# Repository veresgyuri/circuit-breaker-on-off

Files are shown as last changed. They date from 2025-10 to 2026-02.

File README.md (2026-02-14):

# circuit-breaker-on-off
CircuitPython test code for a spring charging motor of the high-voltage circuit breaker

**Status:** Project closed / finalized by Gyuri on 2026-02-14

**Disclaimer:**  
This is an independent, non-manufacturer document.  
See [SAFETY_AND_LEGAL.md](SAFETY_AND_LEGAL.md) for full legal and safety information.

Sorry folks, this repo comes with Hungarian comments only 🙂

# --- KÖF megszakító – felhúzómotor tesztelése ---

**Jogi figyelmeztetés:**  
Ez egy független, nem gyártói anyag.  
A teljes jogi és biztonsági információkat [itt olvashatod](SAFETY_AND_LEGAL.md).

**Az alapprobléma:**  
A rugófelhúzó egységben, idővel elreped az egyik fröccsöntött fogaskerék.

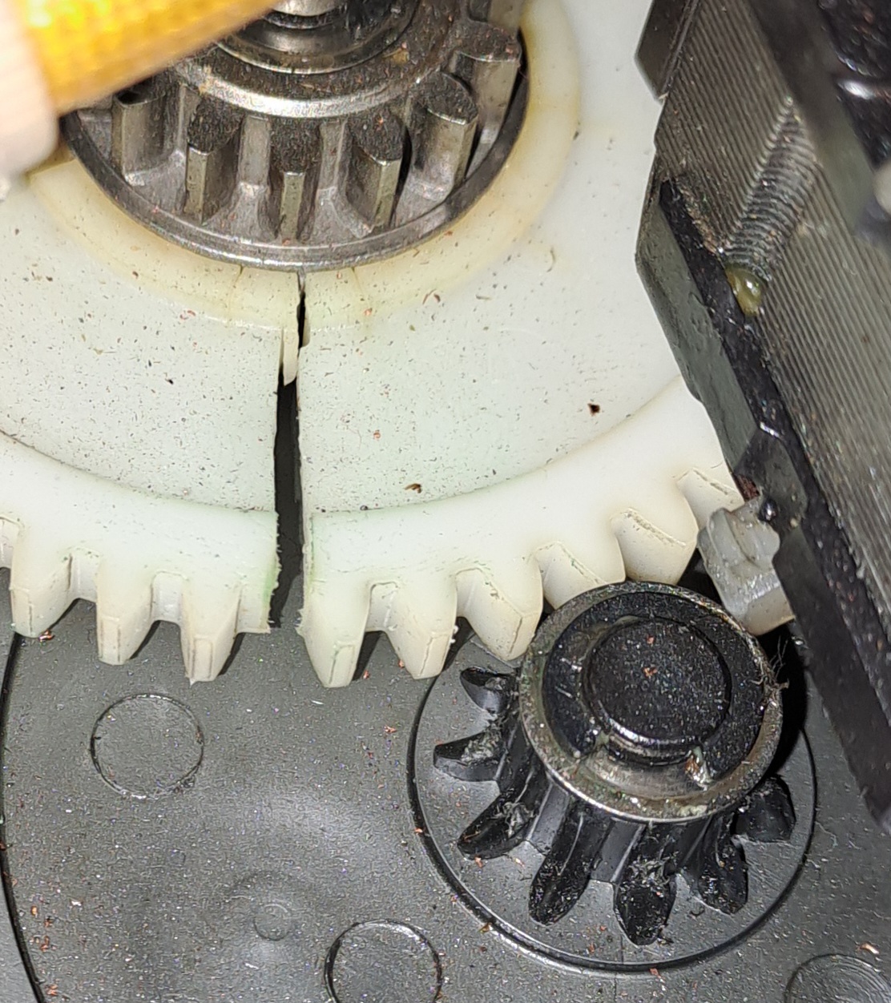
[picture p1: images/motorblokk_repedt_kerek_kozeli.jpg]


**Egy lehetséges megoldás:**  
3D nyomtatott műanyag fogaskerékre cseréljük a hibás alkatrészt.

**Tesztelés:**  
Folyamatos KI-BE kapcsolásokkal nyúzzuk a rugóerőtároló egység felhúzó motorját.

# A cél annak kiderítése, hogy a 3D nyomtatott fogaskerék anyagválasztása sikeres volt-e.

Hardver: ESP32-S3-Zero mikrovezérló

Szoftver: CircuitPython 10.x

A CircuitPython jelenleg a legdinamikusabban fejlődő programozási nyelv a DIY kategóriában (2025. okt.)

Ebben a repóban a tesztelő szoftver életútjáról is találsz verziókövető leírásokat.
Ha ötleted van, vagy hibát találsz, bátran jelezd!

---
Egy kis vizuális betekintés

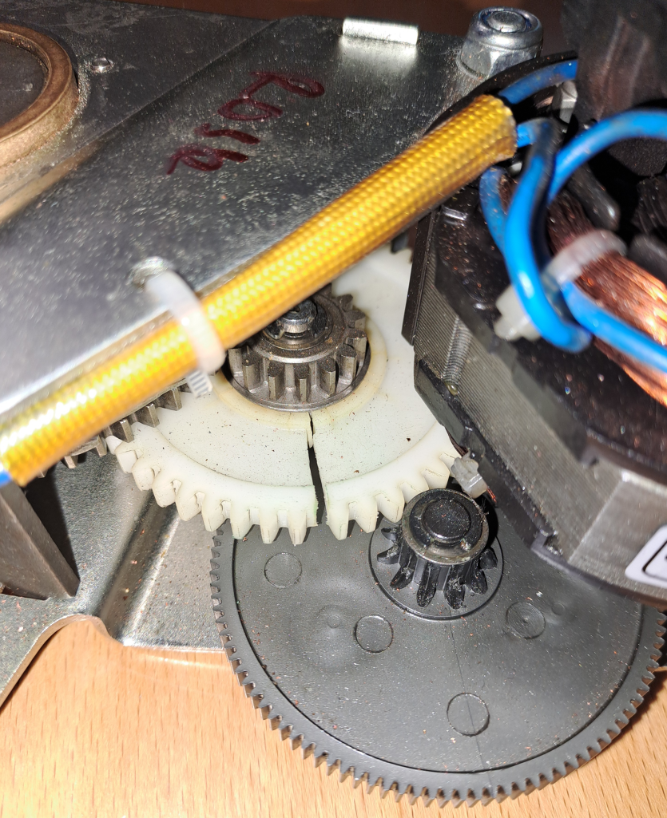
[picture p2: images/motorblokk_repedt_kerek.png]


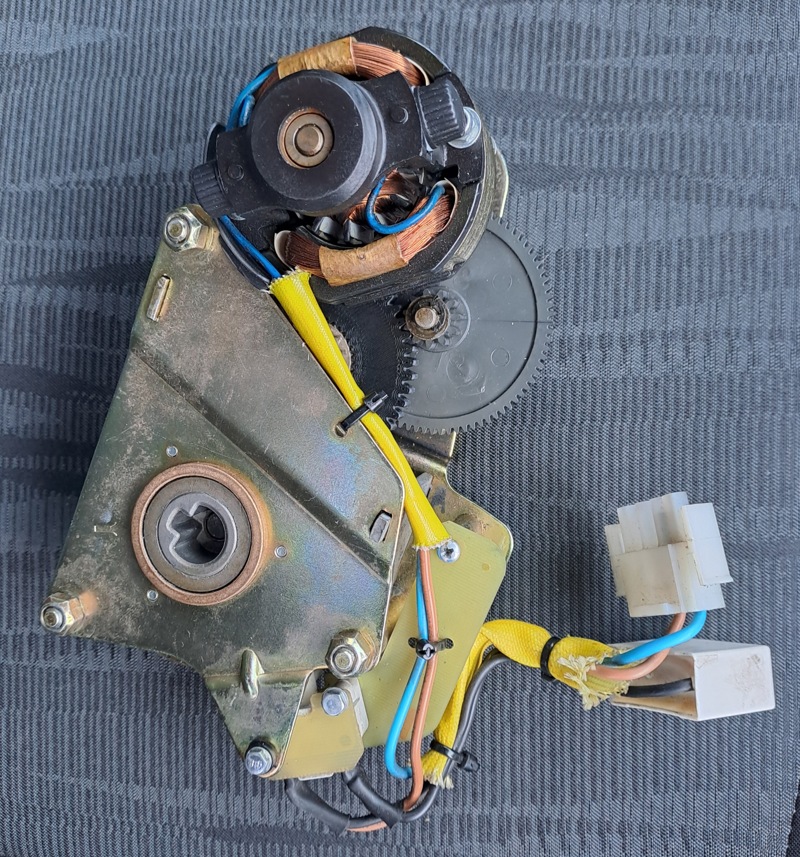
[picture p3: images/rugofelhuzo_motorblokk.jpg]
Motorblokk


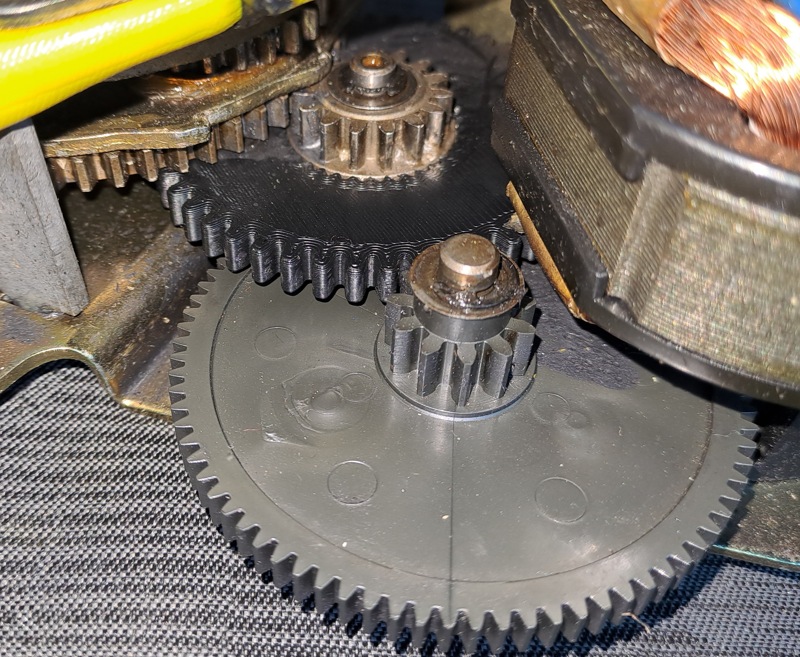
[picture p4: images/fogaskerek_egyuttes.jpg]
Fogaskerekek


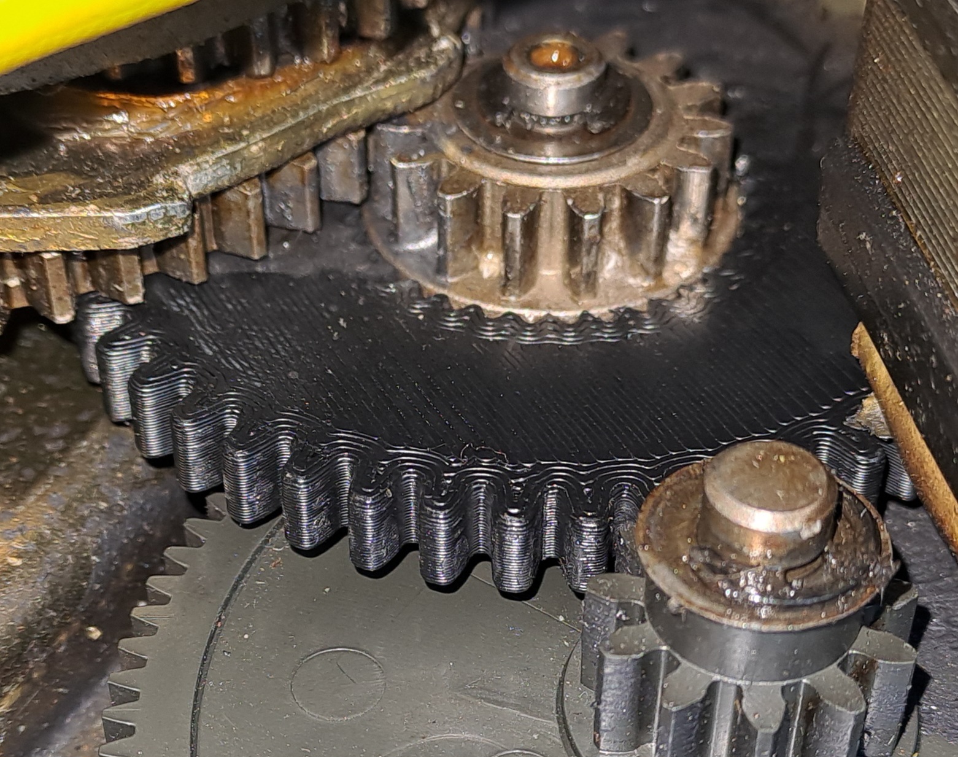
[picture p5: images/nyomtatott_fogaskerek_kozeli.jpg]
Új kerék


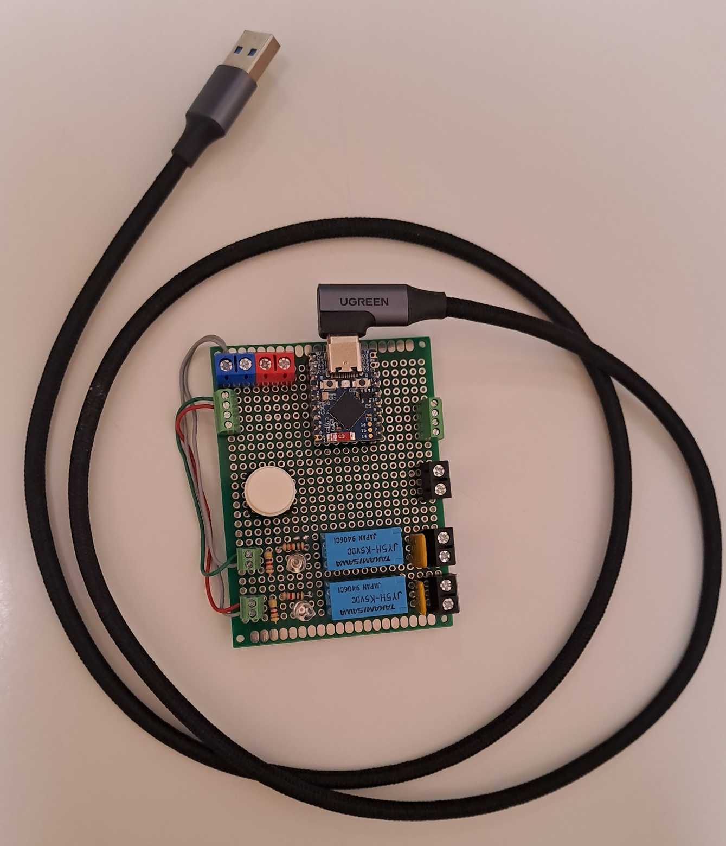
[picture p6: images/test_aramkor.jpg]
0v9 áramkör


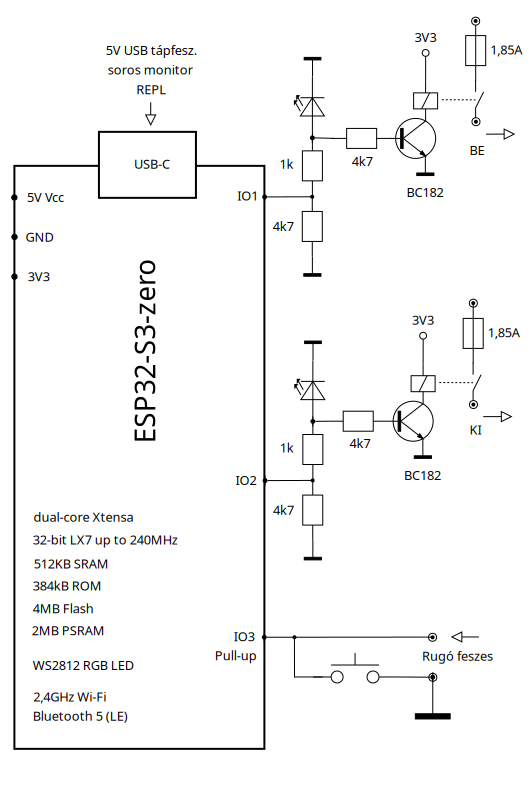
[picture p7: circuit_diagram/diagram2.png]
kapcsolási rajz-2


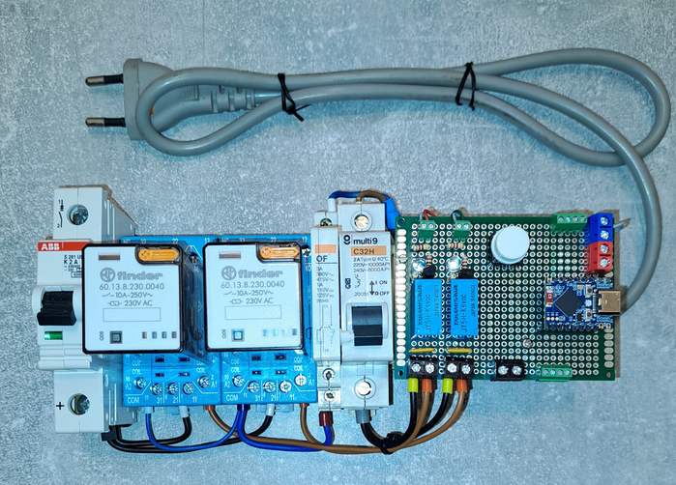
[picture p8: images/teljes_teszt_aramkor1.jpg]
4 relés megoldás AC-DC


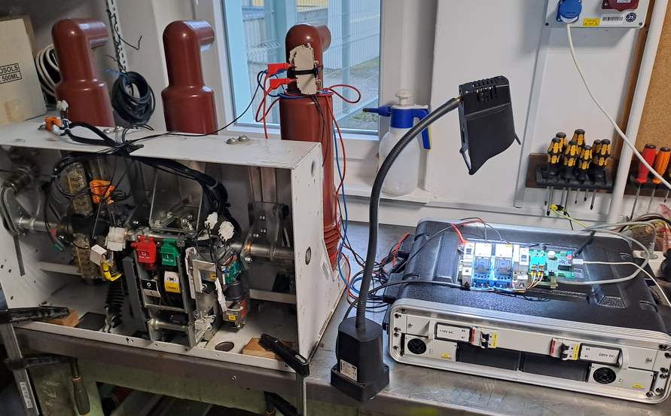
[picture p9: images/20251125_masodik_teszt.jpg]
Indul a tesztelés...


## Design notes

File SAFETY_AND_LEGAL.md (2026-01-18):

1️⃣ (HU) Projekt áttekintés

Ez a repository egy független műszaki vizsgálat és javítási kísérlet dokumentációja, amely egy
középfeszültségű vákuum megszakító működtető mechanizmusához kapcsolódik.
A tartalom saját méréseken, megfigyeléseken és saját készítésű fotókon alapul egy hibás, bontott készülék felhasználásával.

Jogi nyilatkozat

Ez a projekt nem áll kapcsolatban a gyártóval, és nem gyártói jóváhagyású vagy támogatott anyag.
Minden megnevezés és hivatkozás (amennyiben előfordul) kizárólag azonosítási célt szolgál.

A leírt eljárások veszélyes elektromechanikus rendszereket érintenek.
A szerző nem vállal felelősséget semmilyen kárért, balesetért vagy jogszabályi megfelelés hiányáért, amely a tartalom felhasználásából ered.

Az anyag kizárólag megfelelő képesítéssel rendelkező szakemberek számára készült.

2️⃣ (EN) Project overview

This repository documents an independent technical investigation and repair experiment related to the operating mechanism of a medium-voltage vacuum circuit breaker.
The content is based on own measurements, observations, and photographs of a faulty unit used for testing.

Disclaimer

This project is not affiliated with, endorsed by, or supported by any manufacturer.
All trademarks, product names, and references (if mentioned) are used solely for identification purposes.

The described procedures involve electromechanical and high-energy systems and may present serious risks.
The author assumes no responsibility for any damage, injury, or regulatory non-compliance resulting from the use of this information.

This material is intended for qualified professionals only.


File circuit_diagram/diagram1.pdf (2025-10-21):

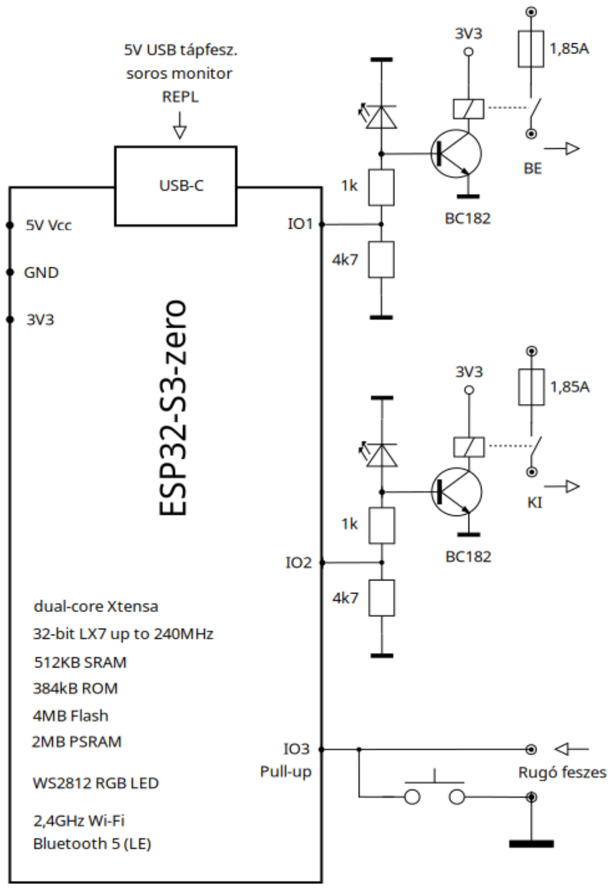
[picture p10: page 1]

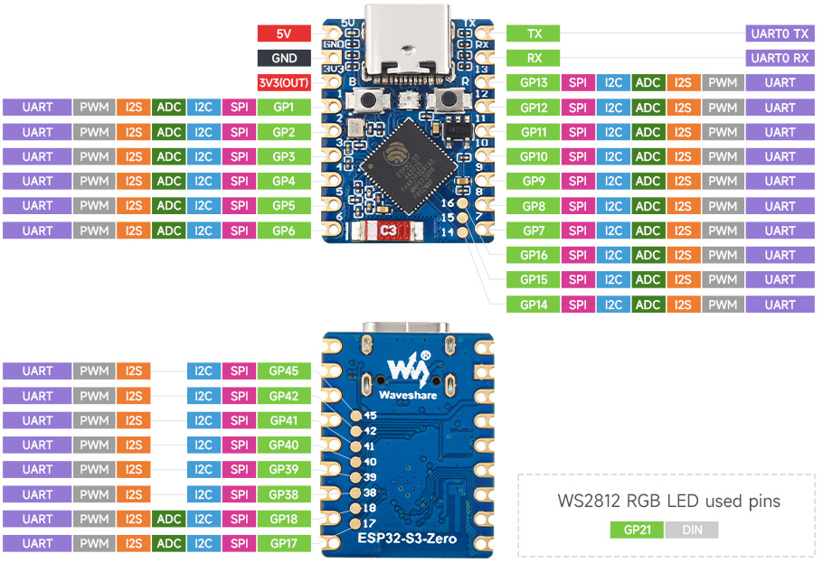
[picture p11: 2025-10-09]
images/ESP32_S3_zero_pinout.png

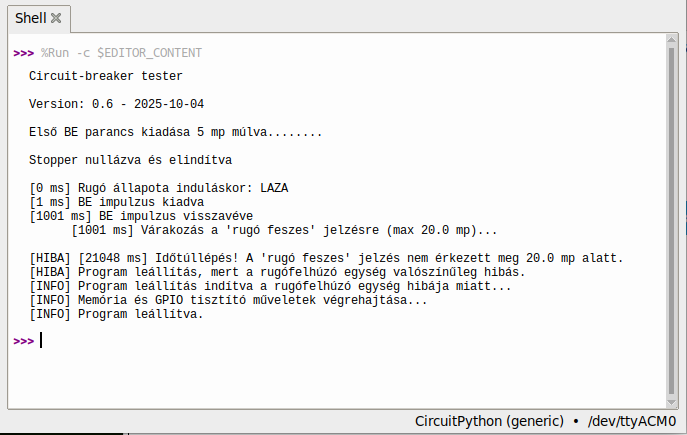
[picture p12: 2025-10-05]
images/0v6_prg_indulas_laza_rugoval.png

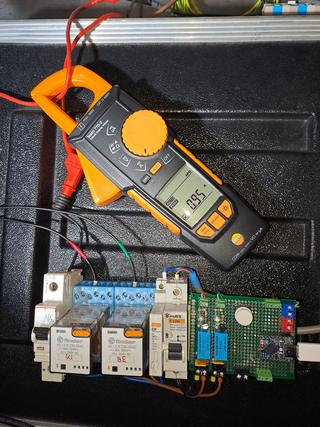
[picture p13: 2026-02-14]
images/motoraram_merese.jpg

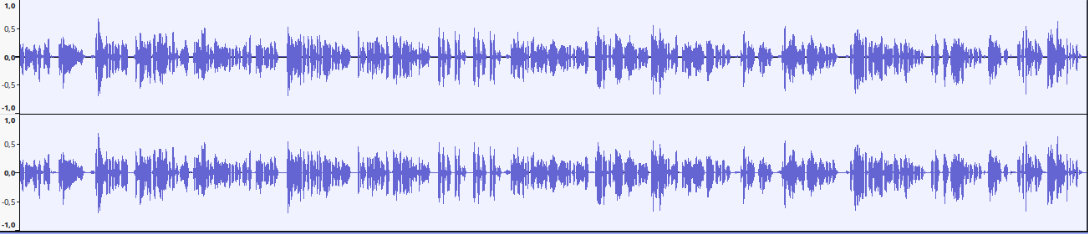
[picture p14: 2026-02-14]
images/temp/Kép2_hang.png

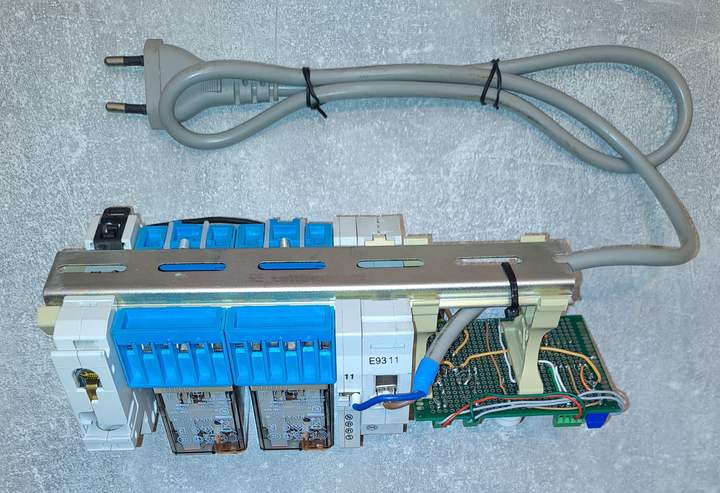
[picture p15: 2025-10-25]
images/teljes_teszt_aramkor3.jpg

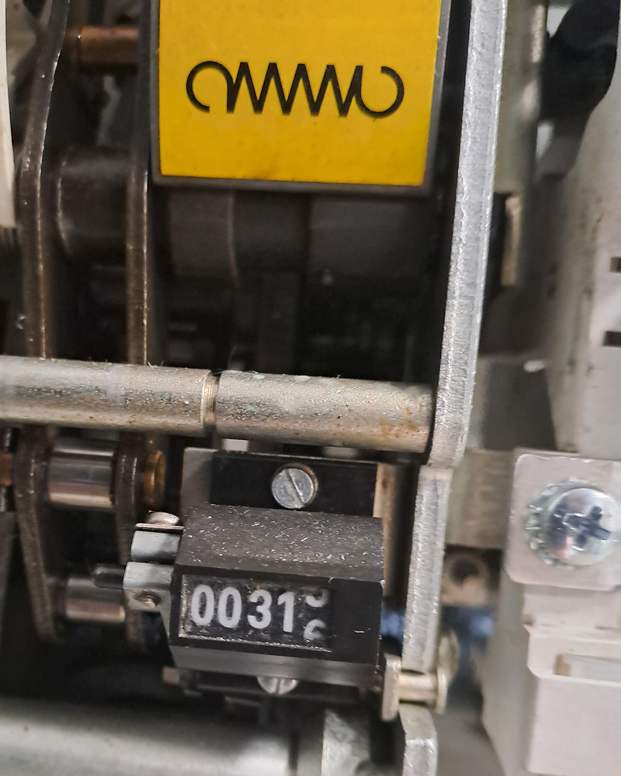
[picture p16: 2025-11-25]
images/20251113_ind_szamlalo_316.jpg

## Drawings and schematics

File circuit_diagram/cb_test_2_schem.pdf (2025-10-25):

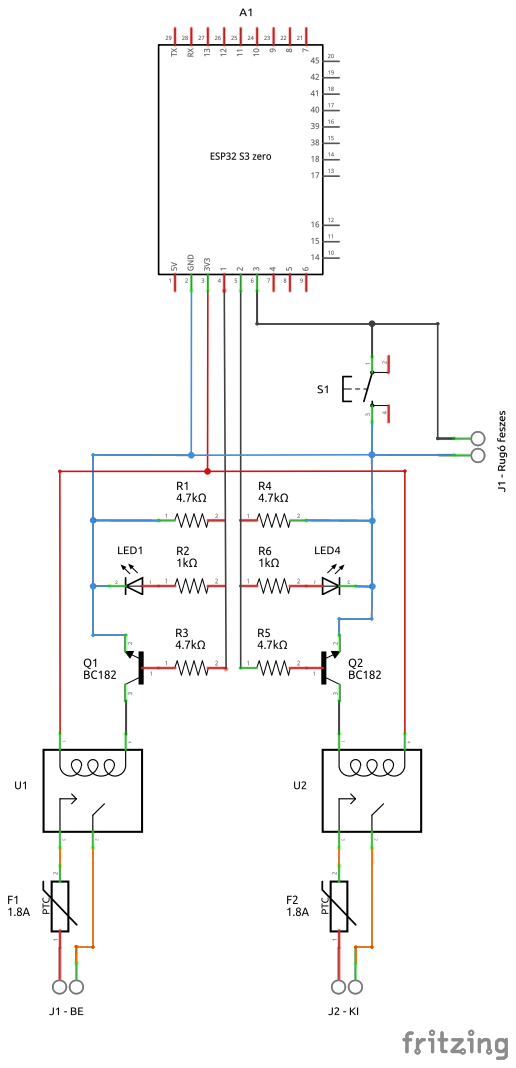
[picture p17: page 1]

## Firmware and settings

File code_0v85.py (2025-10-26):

# code.py - Megszakító (BE/KI) pulzusgenerátor CircuitPython alatt


""" ************ KAPCSOLÁSI RAJZ ******************

 TÁPFESZÜLTSÉG
     REPL         
      ↓          GND
                   │
    USB-C         ┌┴┐ 
┌────┬──┬────┐    4.7k
│    └──┘    ├    └┬┘
│         IO1├─────┴──[1.0k]───→ BE
│            │  
│         IO2├─────┬──[1.0k]───→ KI   
│            │    ┌┴┐
│   ESP32    │    4.7k
│  S3-zero   │    └┬┘
│            │     │
│            │    GND
│    Pull up │   
│         I03├──────── RUGÓ FESZES
│            │
└────────────┘
        
"""

# ver 0.1 - 2025-10-02 minimál kód
# ver 0.2 - 2025-10-02 REPL bevezetése, soros monitorra írjuk a KI-BE eseményeket, ms időbélyeggel
# ver 0.22  2025-10-03 REPL kiegészítés impulzus hossz időkkel
# ver 0.3 - 2025-10-02 Rugó feszes bemenet
# ver 0.4 - Rugó feszes input nem kell (ZöldiZ.) + hibakezelés beépítése
# ver 0.45  REPL üzenet véglegesítés + GPIO deinit, tisztítás
# ver 0.5 - működés -ciklus- számláló beépítése
       # zsákutca, mert a rugó feszes jelzés figyelése nélkül nem tudjuk,
       # hogy valós működés zajlott-e (csak a mi KI-BE ciklusunkat számoljuk)
# ver 0.6 - Rugó feszes IO3 implementálás és a ciklus-számlálóhoz kötése
       # Az első BE-KI ciklus indulása nem függ a 'Rugó feszes' jelzés meglététől
       # ez az utolsó OOP - objektumorientált verzió, mert áttérünk a moduláris eljárásra

# ver 0.7 - 1st funkcionális változat, moduláris eljárásorientáltságra állás 2025-10-05
# ver 0.8 - rugó felhúzási idő mérése, logolása
# ver 0.85  hibajavítások, duplikálások törlése 2025-10-26

import board
import digitalio
import time


VERSION = "0.85 - javítások - 2025-10-26"

# PIN-ek
BE_PIN = board.IO1
KI_PIN = board.IO2
RUGO_FESZES_PIN = board.IO3

# Konstansok - időzítések (sec)
PULSE = 1.0
WAIT_AFTER_BE = 20.0
WAIT_AFTER_KI = 10.0
BOOT_DELAY = 5.0
RUGO_FESZES_TIMEOUT = 20.0
DEBOUNCE_MS = 50 # ms, stabil állapot ideje
POLL_INTERVAL = 0.01 # sec, mintavételi intervallum
ENSURE_LAZA_TIMEOUT = 1.0  # max ennyit várunk, hogy LAZA legyen (sec)

# Logikai beállítások
RUGO_ACTIVE_LOW = True  # ha True, akkor LOW = FESZES

# Állapotok
be = ki = rugo = None
cycle_count = 0

def now_ms():
    return int((time.monotonic() - t0) * 1000)

def log(msg):
    print(f"[{now_ms()} ms] {msg}")

def init_pins():
    global be, ki, rugo
    be = digitalio.DigitalInOut(BE_PIN)
    be.direction = digitalio.Direction.OUTPUT
    be.value = False

    ki = digitalio.DigitalInOut(KI_PIN)
    ki.direction = digitalio.Direction.OUTPUT
    ki.value = False

    rugo = digitalio.DigitalInOut(RUGO_FESZES_PIN)
    rugo.direction = digitalio.Direction.INPUT
    rugo.pull = digitalio.Pull.UP

def deinit_pins():
    global be, ki, rugo
    try:
        if be is not None:
            be.value = False
            be.deinit()
        if ki is not None:
            ki.value = False
            ki.deinit()
        if rugo is not None:
            rugo.deinit()
    except Exception:
        # biztos tisztítás; csak logolunk, nem áll le a programfutás
        print("Tisztítás közben hiba történt.")

def pulse(pin_obj, duration):
    pin_obj.value = True
    time.sleep(duration)
    pin_obj.value = False

def rugo_feszes():
    # visszaadja True/False attól függően, hogy a jel aktív-e
    val = rugo.value
    return (not val) if RUGO_ACTIVE_LOW else val

def wait_for_feszes(timeout, debounce_ms=DEBOUNCE_MS):
    """Vár a FESZES (active) állapotra, csak ha az stabilan fennáll debounce_ms ideig."""
    start = time.monotonic()
    stable_needed = debounce_ms / 1000.0
    stable_start = None
    while time.monotonic() - start < timeout:
        cur = rugo_feszes()  # True = FESZES
        if cur:
            if stable_start is None:
                stable_start = time.monotonic()
            elif time.monotonic() - stable_start >= stable_needed:
                return True
        else:
            stable_start = None
        time.sleep(POLL_INTERVAL)
    return False

def measure_rugo_felhuzasi_ido(max_timeout):
    """
    Mér egy LAZA -> FESZES átmenetet: ha már FESZES -> 0.0, 
    ha nem történik meg max_timeout alatt -> None,
    különben visszaadja a felhúzási időt másodpercben.
    """
    # Ha már feszes, visszaadjuk 0.0 (azonnali)
    if rugo_feszes():
        return 0.0

    # Győződjünk meg róla, hogy LAZA állapotból indulunk (max ENSURE_LAZA_TIMEOUT)
    ensure_start = time.monotonic()
    while time.monotonic() - ensure_start < ENSURE_LAZA_TIMEOUT:
        if not rugo_feszes():  # LAZA
            break
        time.sleep(POLL_INTERVAL)

    # Start időpont (innen mérünk)
    t_start = time.monotonic()

    # Várjuk a debounce-olt FESZES állapotot
    if wait_for_feszes(max_timeout):
        return time.monotonic() - t_start
    return None

def main_loop():
    global cycle_count, t0
    # Nullpont indítása a loop elején (egységes ms méréshez)
    t0 = time.monotonic()

    log("Circuit-breaker tester")
    log(f"Version: {VERSION}")
    log(f"Első BE parancs {BOOT_DELAY} mp múlva")
    time.sleep(BOOT_DELAY)

    log("Stopper nullázva és elindítva")
    log(f"Rugó állapota induláskor: {'FESZES' if rugo_feszes() else 'LAZA'}")

    while True:
        # --- BE impulzus ---
        log("BE impulzus kiadva")
        pulse(be, PULSE)
        log("BE impulzus visszavéve")

        # --- Rugó felhúzási idő mérése (LAZA -> FESZES) ---
        log(f"Rugó felhúzási idő mérése (max {RUGO_FESZES_TIMEOUT} s)...")
        elapsed = measure_rugo_felhuzasi_ido(RUGO_FESZES_TIMEOUT)
        if elapsed is None:
            log(f"[HIBA] Időtúllépés! A LAZA -> FESZES átmenet nem történt meg {RUGO_FESZES_TIMEOUT} s alatt.")
            raise SystemExit("Rugófelhúzó egység hibás?")
        else:
            ms = int(elapsed * 1000)
            log(f"Rugó felhúzási idő: {ms} ms")
            cycle_count += 1

        # --- Várakozás BE után, majd KI impulzus ---
        log(f"KI impulzus {WAIT_AFTER_BE} mp múlva........")
        time.sleep(WAIT_AFTER_BE)

        log("KI impulzus kiadva")
        pulse(ki, PULSE)
        log("KI impulzus visszavéve")

        # --- Ciklus összegzés és várakozás a következő BE-ig ---
        log(f"===== BE-KI ciklus befejezve. Eddig {cycle_count} rugófelhúzás volt =====")
        log(f"BE impulzus {WAIT_AFTER_KI} mp múlva........")
        time.sleep(WAIT_AFTER_KI)


if __name__ == "__main__":
    try:
        init_pins()
        main_loop()
    except KeyboardInterrupt:
        log("Program megszakítva a felhasználó által.")
    except SystemExit as e:
        log("Program leállítás indítva: " + str(e))
    except Exception as e:
        log("Váratlan hiba történt: " + repr(e))
        traceback.print_exc()
    finally:
        log("Memória és GPIO tisztítás...")
        deinit_pins()
        log("Program leállítva.")

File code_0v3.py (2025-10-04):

# code.py - egyszerű megszakító (BE/KI) pulzusgenerátor CircuitPython alatt
# code.py - egyszerű megszakító (BE/KI) pulzusgenerátor CircuitPython alatt
# ver 0.1 - 2025-10-02 minimál
# ver 0.2 - 2025-10-02 REPL bevezetése
# soros monitorra írjuk a KI-BE eseményeket, ms időbélyeggel
# ver 0.22 - 2025-10-03 REPL kiegészítés impulzus hossz időkkel
# ver 0.3 - 2025-10-02 Rugó feszes bemenet

import board
import digitalio
import time

VERSION = "0.3 - 2025-10-02"

# --- GPIO PIN ---
BE_PIN = board.GPIO1   # megszakító BE
KI_PIN = board.GPIO2   # megszakító KI
RUGO_PIN = board.GPIO3 # rugó feszes bemenet

# --- Times [sec] ---
PULSE = 1.0
WAIT_AFTER_BE = 20.0
WAIT_AFTER_KI = 10.0
BOOT_DELAY = 0.5  # rövid várakozás boot után

#  --- Kiírjuk a verziót induláskor ---
print("Circuit-breaker tester")
print("VERSION:", VERSION)

# --- pin inicializálás ---
be = digitalio.DigitalInOut(BE_PIN)
be.direction = digitalio.Direction.OUTPUT
be.value = False

ki = digitalio.DigitalInOut(KI_PIN)
ki.direction = digitalio.Direction.OUTPUT
ki.value = False

# Rugó bemenet inicializálása
rugo = digitalio.DigitalInOut(RUGO_PIN)
rugo.direction = digitalio.Direction.INPUT
# Állítsd Pull.UP vagy Pull.DOWN szerint, itt alap: Pull.DOWN (aktív = True)
rugo.pull = digitalio.Pull.DOWN

time.sleep(BOOT_DELAY)  # adunk egy kis időt boot után

# Nullapont beállítása (ms felbontás alapja)
t0 = time.monotonic()
print("t0 set")

def now_ms():
    return int((time.monotonic() - t0) * 1000)

# Rugo él-észleléshez állapot tárolása
last_rugo = rugo.value

# Segédfüggvény: várakozás, de közben gyakran ellenőrzi a RUGO bemenetet
def wait_with_rugo(duration, sample_interval=0.05):
    global last_rugo
    end = time.monotonic() + duration
    while time.monotonic() < end:
        cur = rugo.value
        # Rising edge = rugó feszes jel
        if cur and not last_rugo:
            print("[{0} ms] RUGO ASSERTED".format(now_ms()))
        # (opcionális) Falling edge - feloldás
        if not cur and last_rugo:
            print("[{0} ms] RUGO RELEASED".format(now_ms()))
        last_rugo = cur
        # rövid alvás, de ne legyen túl hosszú, hogy ne hagyjunk ki eseményt
        time.sleep(sample_interval)

# --- végtelen ciklus ---
while True:
    # BE impulzus kezdete — kiírás ms pontossággal
    print("[{0} ms] BE pulse start".format(now_ms()))
    be.value = True
    wait_with_rugo(PULSE)   # 1 s alatt is figyelünk a RUGO-ra
    be.value = False

    # 20 s csönd (mindkettő inaktív) — közben RUGO figyelés
    wait_with_rugo(WAIT_AFTER_BE)

    # KI impulzus kezdete — kiírás ms pontossággal
    print("[{0} ms] KI pulse start".format(now_ms()))
    ki.value = True
    wait_with_rugo(PULSE)
    ki.value = False

    # 10 s csönd
    wait_with_rugo(WAIT_AFTER_KI)

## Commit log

2025-10-05 MŰKÖDIK (de ez az utolsó OOP-s verzió)
2025-10-05 Rugófelhúzás - motoridő mérése
2025-10-24 Diagram2, add transistor base resistor
2025-10-25 panel completed
    [vd4_test_1.fzz]
2026-01-18 Rename vd4_test_1.fzz to cb_test_1.fzz
    SAFETY_AND_LEGAL.md
    [cb_test_1.fzz]
2026-02-14 Move diagram1.png to circuit_diagram folder
2026-02-14 Move diagram2.png to circuit_diagram folder
2026-02-14 rename path for circuit diagram.png
2026-02-14 Add current meter picture
